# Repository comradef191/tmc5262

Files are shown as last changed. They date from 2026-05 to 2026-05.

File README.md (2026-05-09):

# TMC5262
This repository contains KiCAD 10.0 files for two stepper-motor driver boards based on the Trinamic [TMC5262](https://www.analog.com/en/products/tmc5262.html) driver.

**Notice:** As of May 9th 2026, these boards have not yet been tested. The initial release of these boards contains the text 'PROTOTYPE' on the silkscreen to reflect this.

You will have errors on opening the files if you do not have the [nasin-nanpa font](https://github.com/ETBCOR/nasin-nanpa) installed, used by me for both marking my name and occasionally eastereggs.

These files contain LCSC P/Ns for the SMD components and, on the external board the two large capacitors. Specific P/Ns are not provided for other through-hole components.

While these files are intended to be compatible with JLCPCB assembly, as of May 9th 2026 only Digikey is [selling the driver IC](https://www.digikey.com/en/products/detail/analog-devices-inc-maxim-integrated/TMC5262AFV/29292344), thus you will have to solder this component yourself or consign the chips to JLCPCB.

## External Driver:
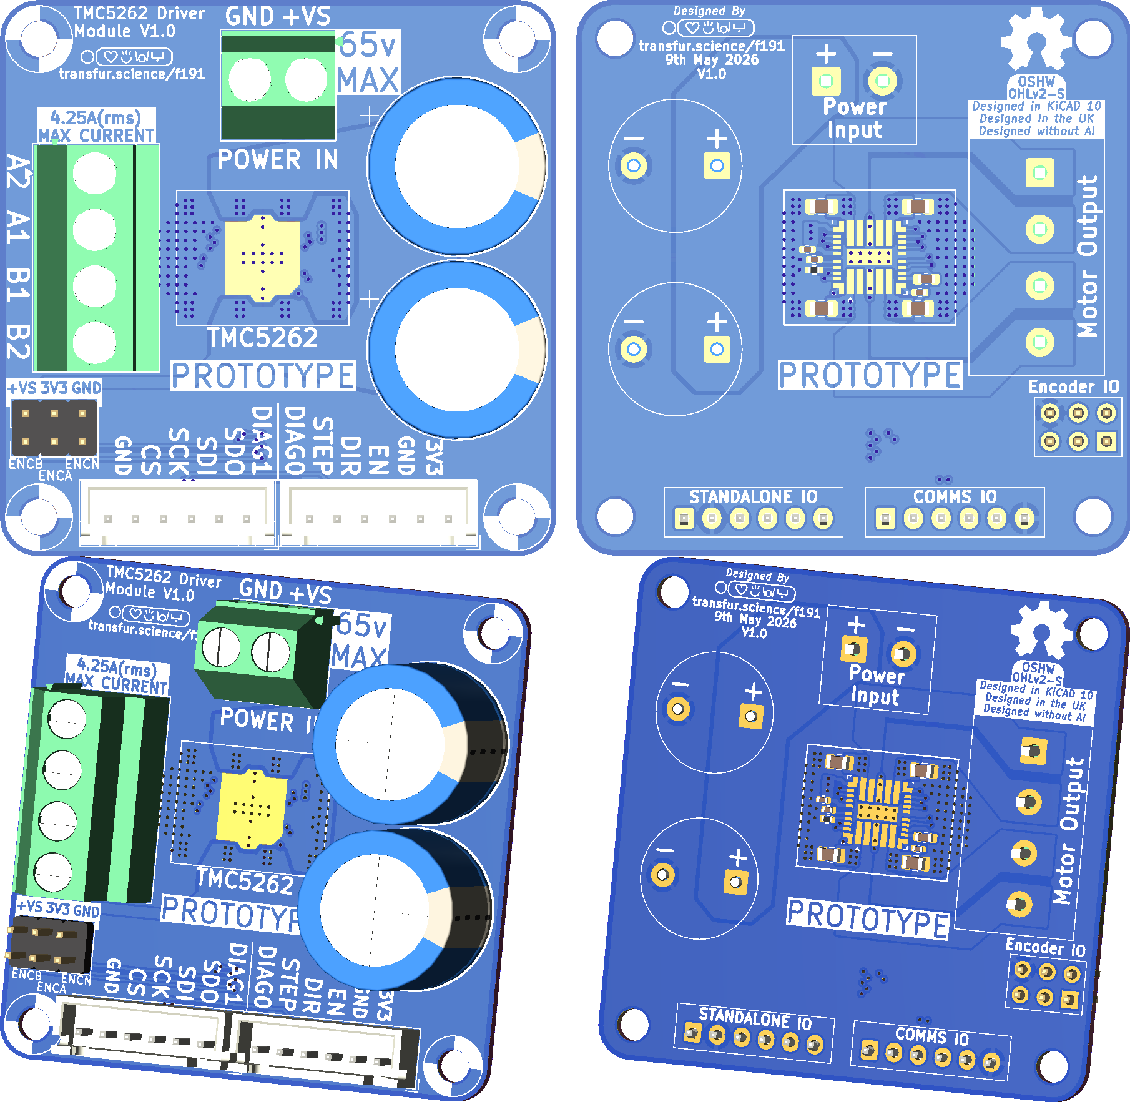
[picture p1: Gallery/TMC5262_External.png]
TMC5262_External

This is a larger board intended for fully-testing the driver and all its features.

The files for this board are located in the *'Motor-TMC5262-external'* directory.

- **Dimensions:** 50x50mm PCB, with 43x3mm M3 mounting holes.
-**Voltage Input:** 65v max, 1x2 5.08mm-Pitch screwterminal
- **Coil Output:** 4A max, 1x4 5.08mm-Pitch screwterminal
- **DIAG0 & DIAG1:** DIAG0 is on the 'STANDALONE IO' connector, DIAG1 is on the 'COMMS IO' connector. Connecting of both or either is not required.
- **Encoder:** ENCN, ENCA, ENCB pins broken-out to 2x3 header
- **Brake Resistor:** None built-in, use header to connect externally
- **Connectivity:** Connects to the MCU using two 6-pin JST-XH connectors

## Stepstick Driver:
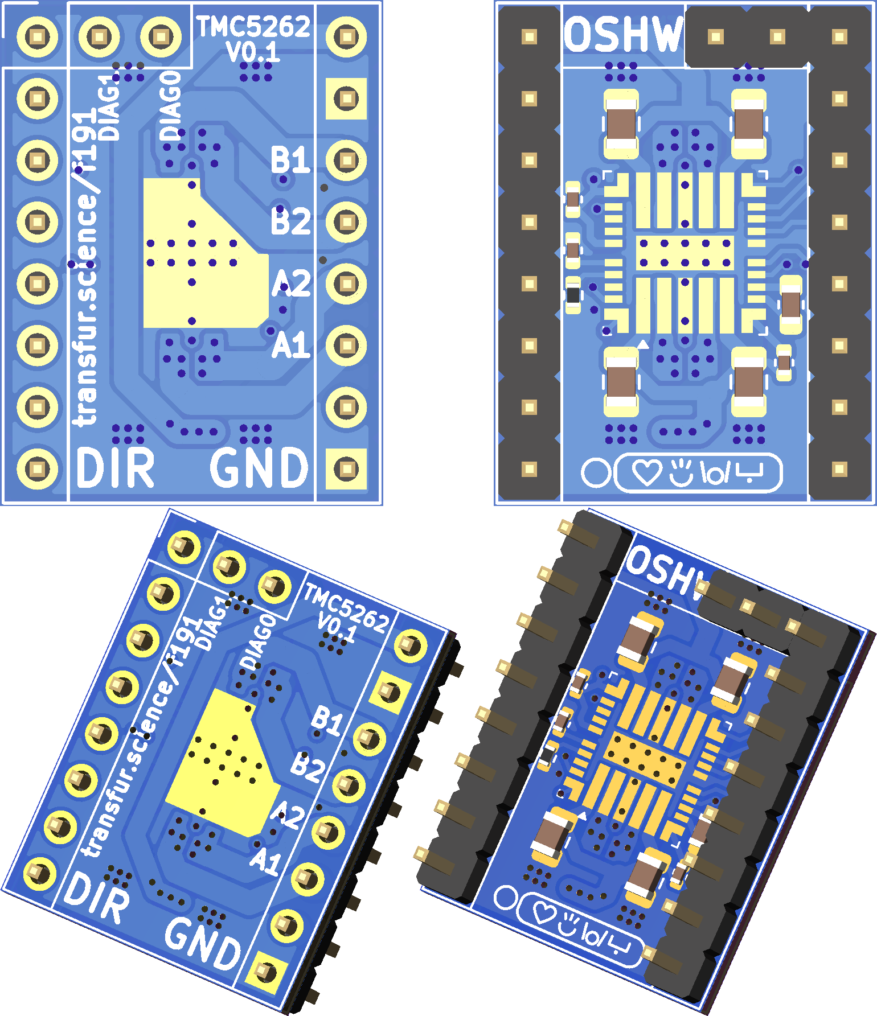
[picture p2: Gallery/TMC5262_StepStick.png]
TMC5262_StepStick

This is a small board intended for testing compatibility with existing stepstick-based mainboards, due to its smaller size caution to ensure no overheating should be taken.

The files for this board are located in the *'Motor-TMC5262-stepstick'* directory.

- **Dimensions:** 15.74x20.82mm StepStick
- **Voltage Input:** 65v max (Do not exceed rating of your mainboard)
- **Coil Output:** 3A max, B1/B2/A2/A1 instead of B2/A2/A1/B1
- **DIAG0 & DIAG1:** DIAG0 & DIAG1 connected per other StepSticks with two DIAG pins (e.g. [TMC22x SilentStepStick](https://learn.watterott.com/silentstepstick/pinconfig/))
- *Encoder:** Not-Present
- **Brake Resistor:** Not-Present
- **Connectivity:** Connects to the MCU using a standard 'StepStick' style socket. Make sure to set the jumpers to use SPI.

# License
This project is licensed under the CERN OHL V2 - S, see LICENSE.TXT for further information.

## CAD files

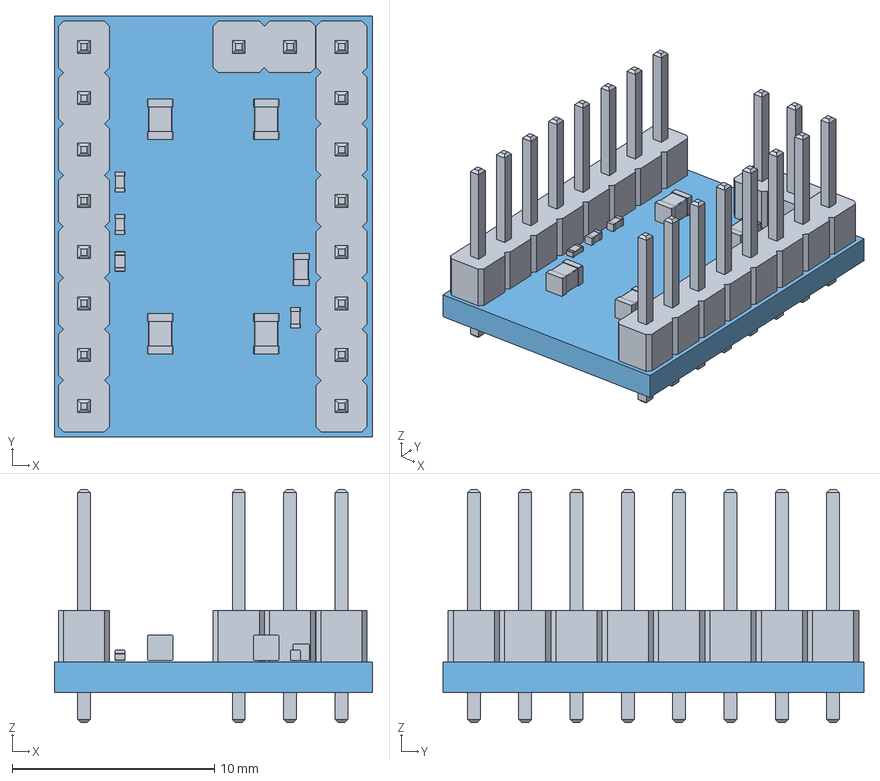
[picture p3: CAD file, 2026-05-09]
Resources/Motor-TMC5262-Stick.step
15.7 x 20.8 x 11.5 mm
C_0805_2012Metric x 4
C_0402_1005Metric x 3
C_0603_1608Metric
R_0402_1005Metric
PinHeader_1x08_P2.54mm_Vertical x 2
PinHeader_1x02_P2.54mm_Vertical
Motor-TMC5262-Stick_PCB

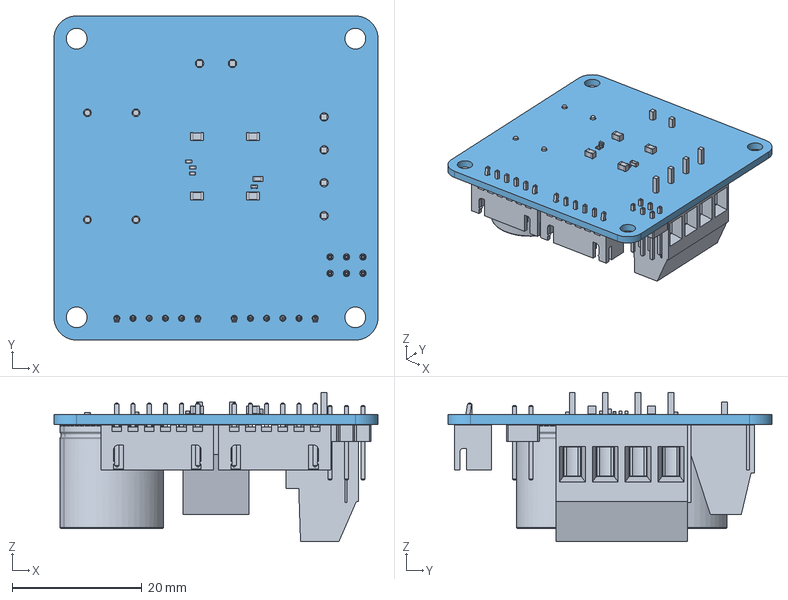
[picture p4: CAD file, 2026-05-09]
Resources/Motor-TMC5262-board.step
50.0 x 50.0 x 23.0 mm
C_0805_2012Metric x 4
C_0402_1005Metric x 3
C_0603_1608Metric
R_0402_1005Metric
JST_XH_B6B-XH-A_1x06_P2.50mm_Vertical x 2
CP_Radial_D16.0mm_P7.50mm x 2
TerminalBlock_Phoenix_MKDS-3-4-5.08_1x04_P5.08mm_Horizontal
PinHeader_2x03_P2.54mm_Vertical
TerminalBlock_Phoenix_MKDS-1,5-2-5.08_1x02_P5.08mm_Horizontal
Motor-TMC5262-board_PCB

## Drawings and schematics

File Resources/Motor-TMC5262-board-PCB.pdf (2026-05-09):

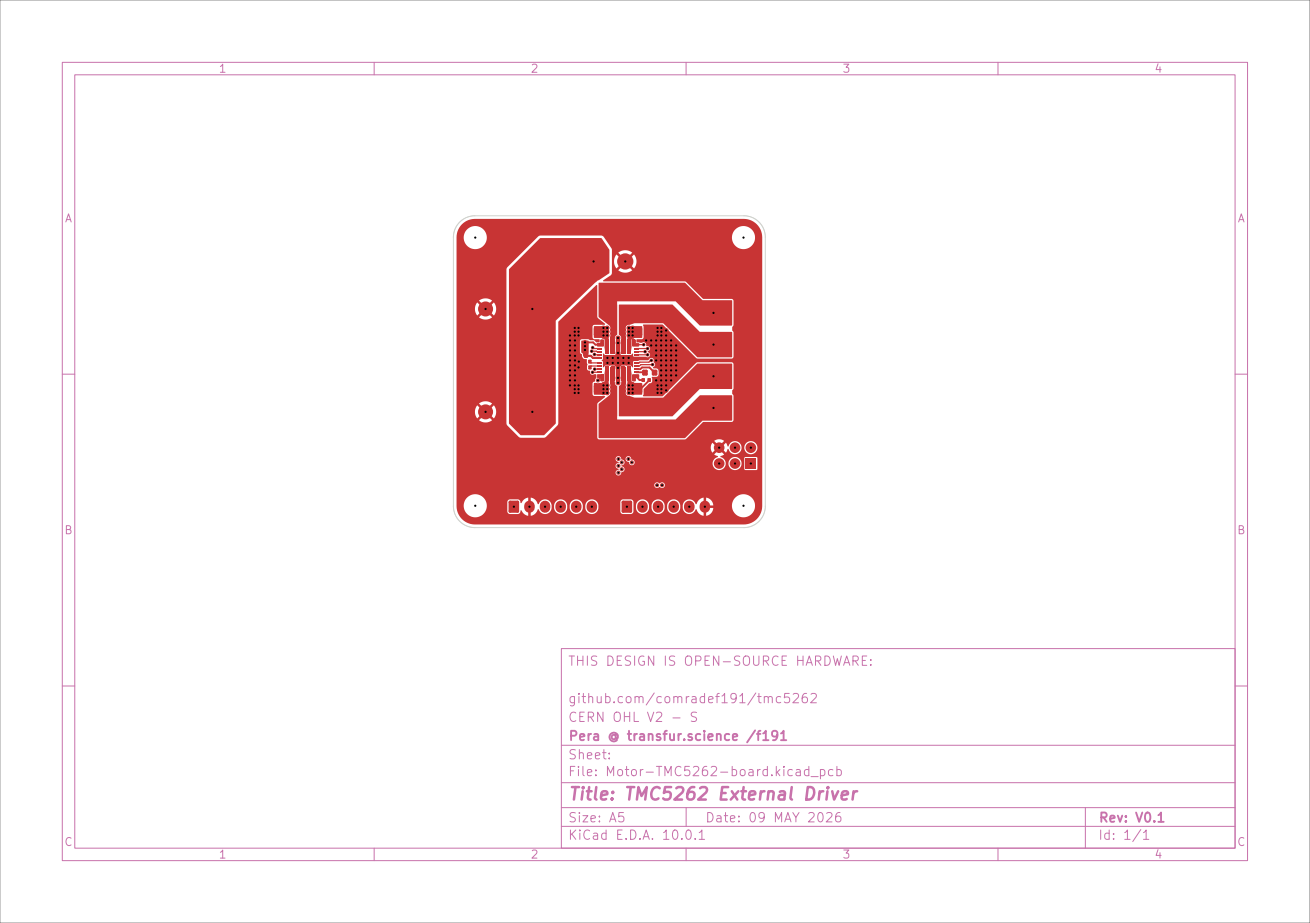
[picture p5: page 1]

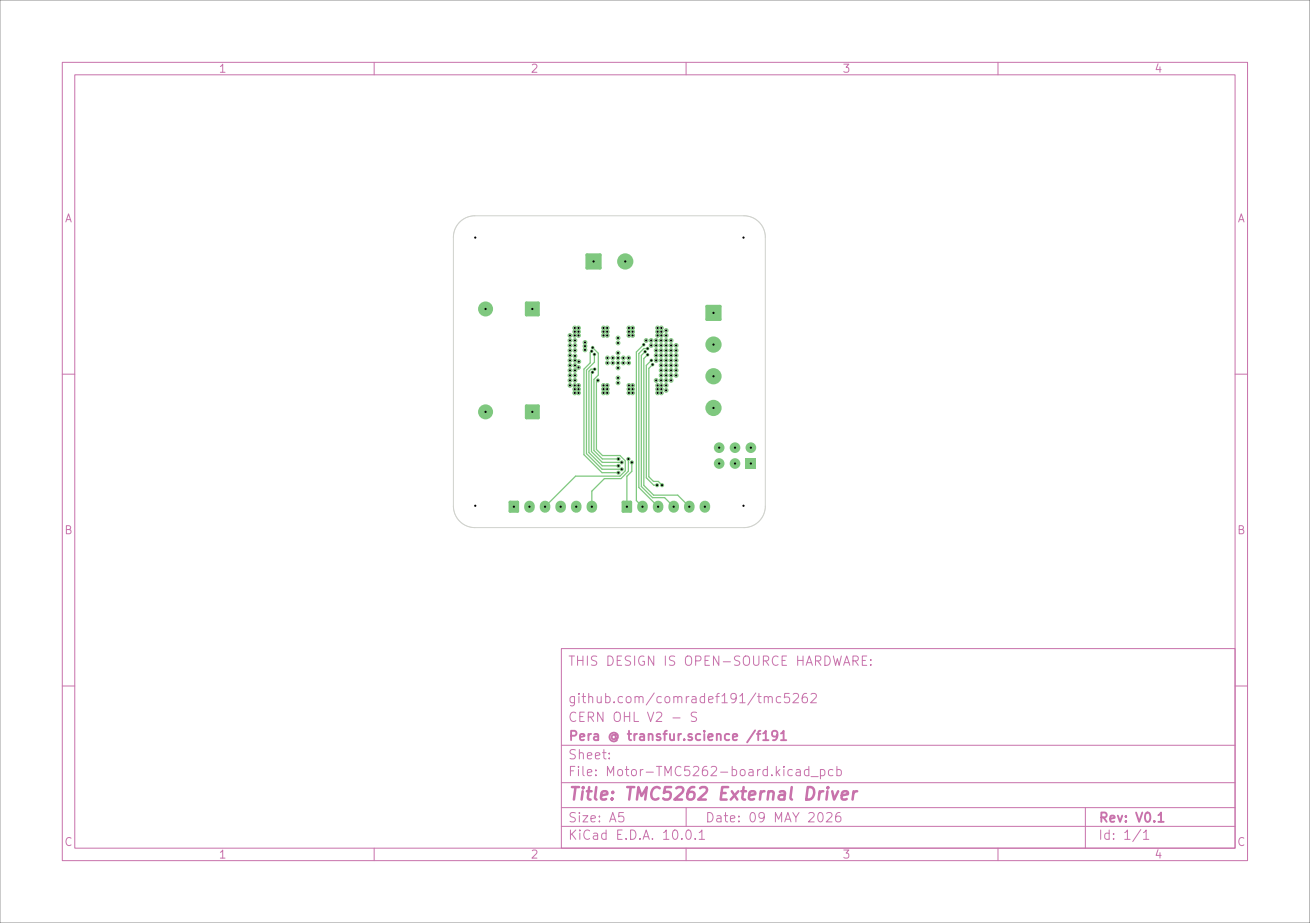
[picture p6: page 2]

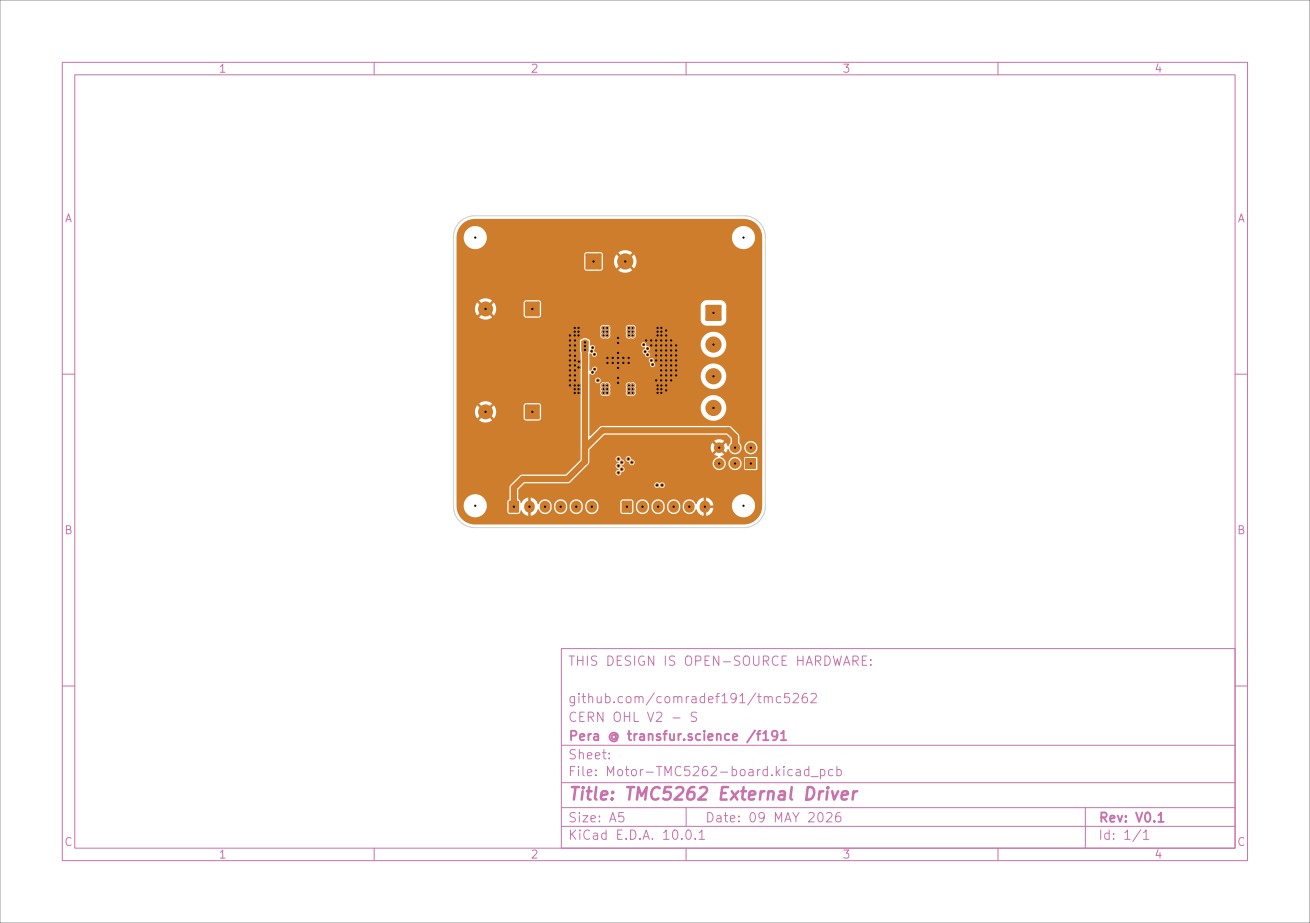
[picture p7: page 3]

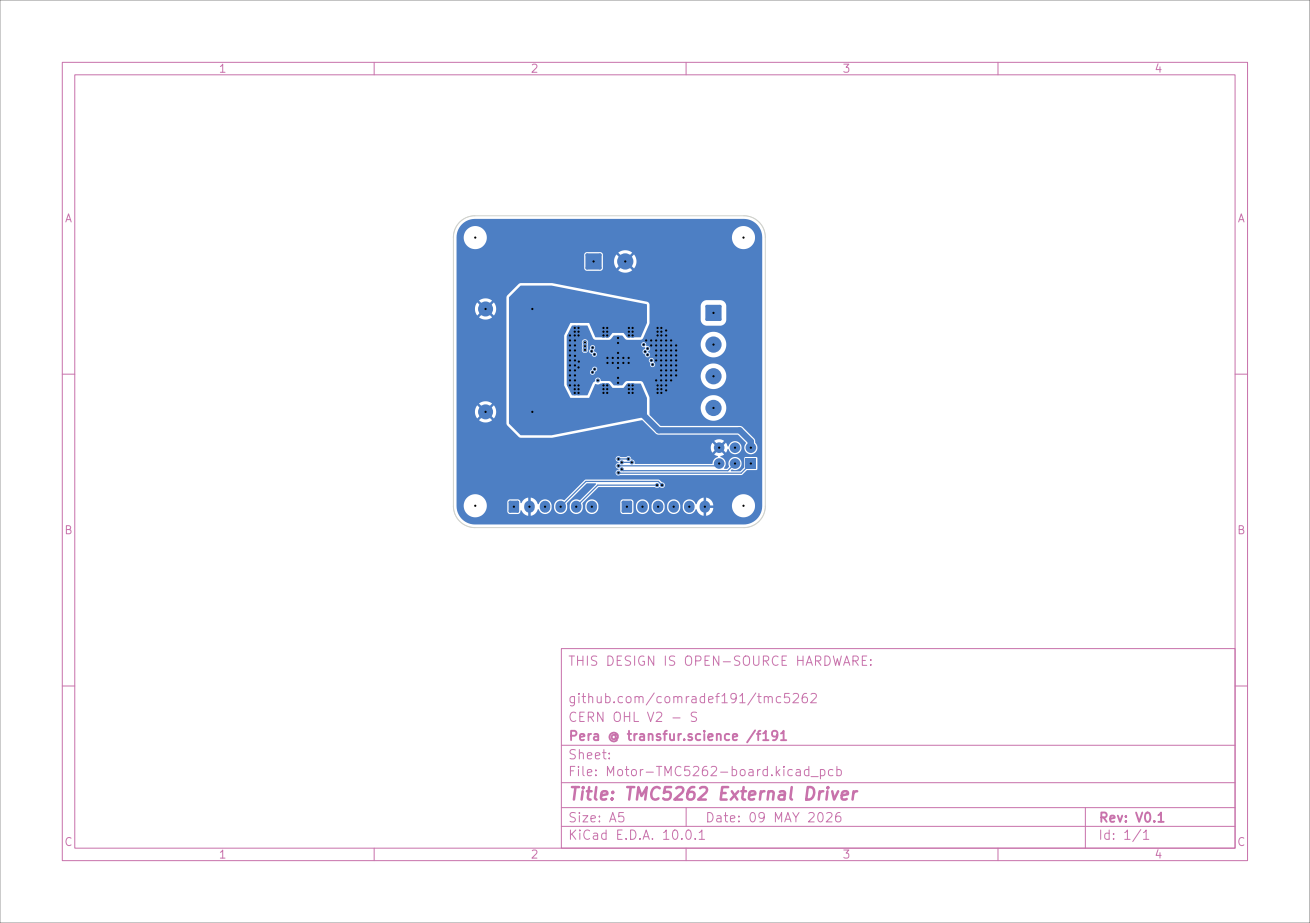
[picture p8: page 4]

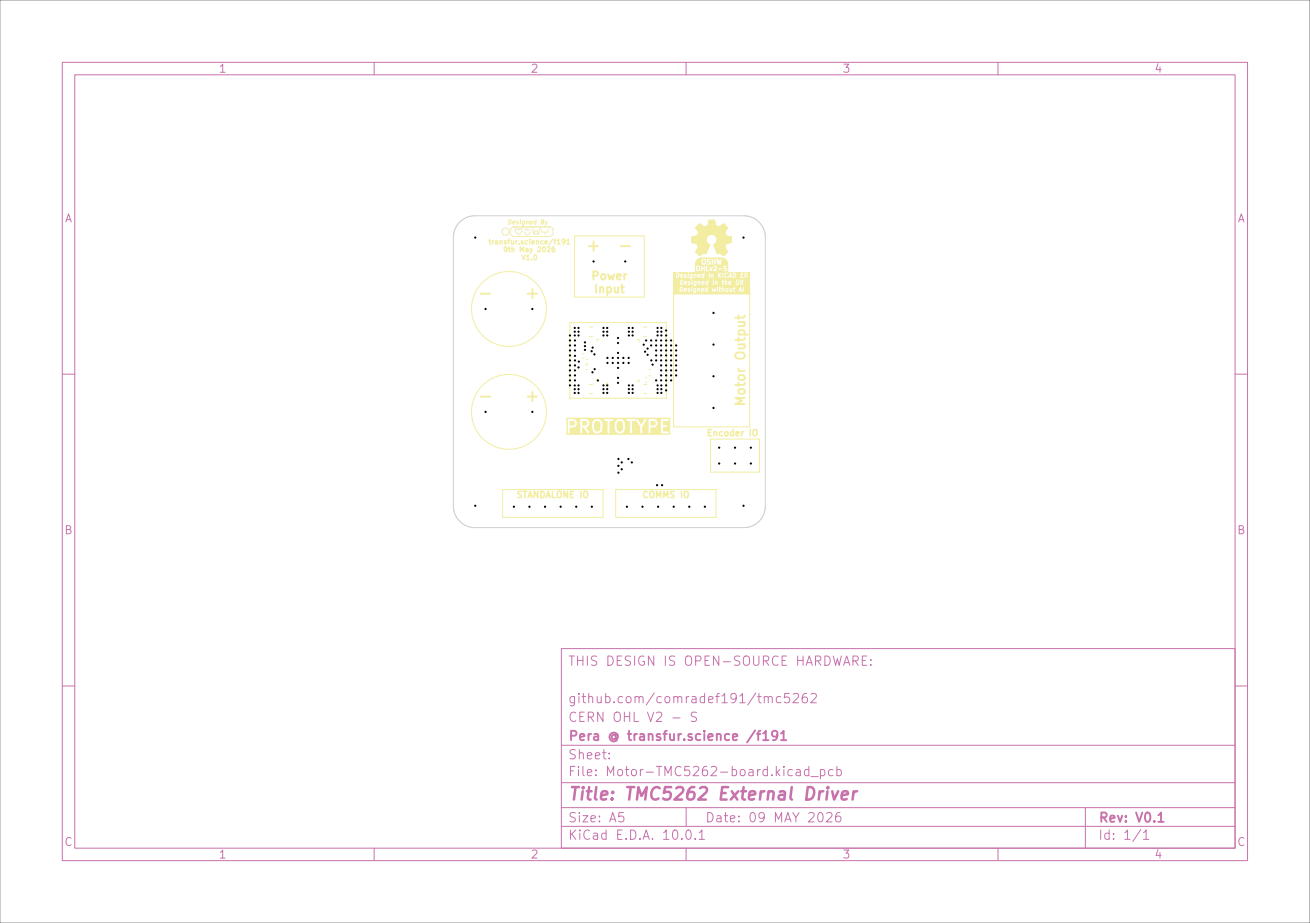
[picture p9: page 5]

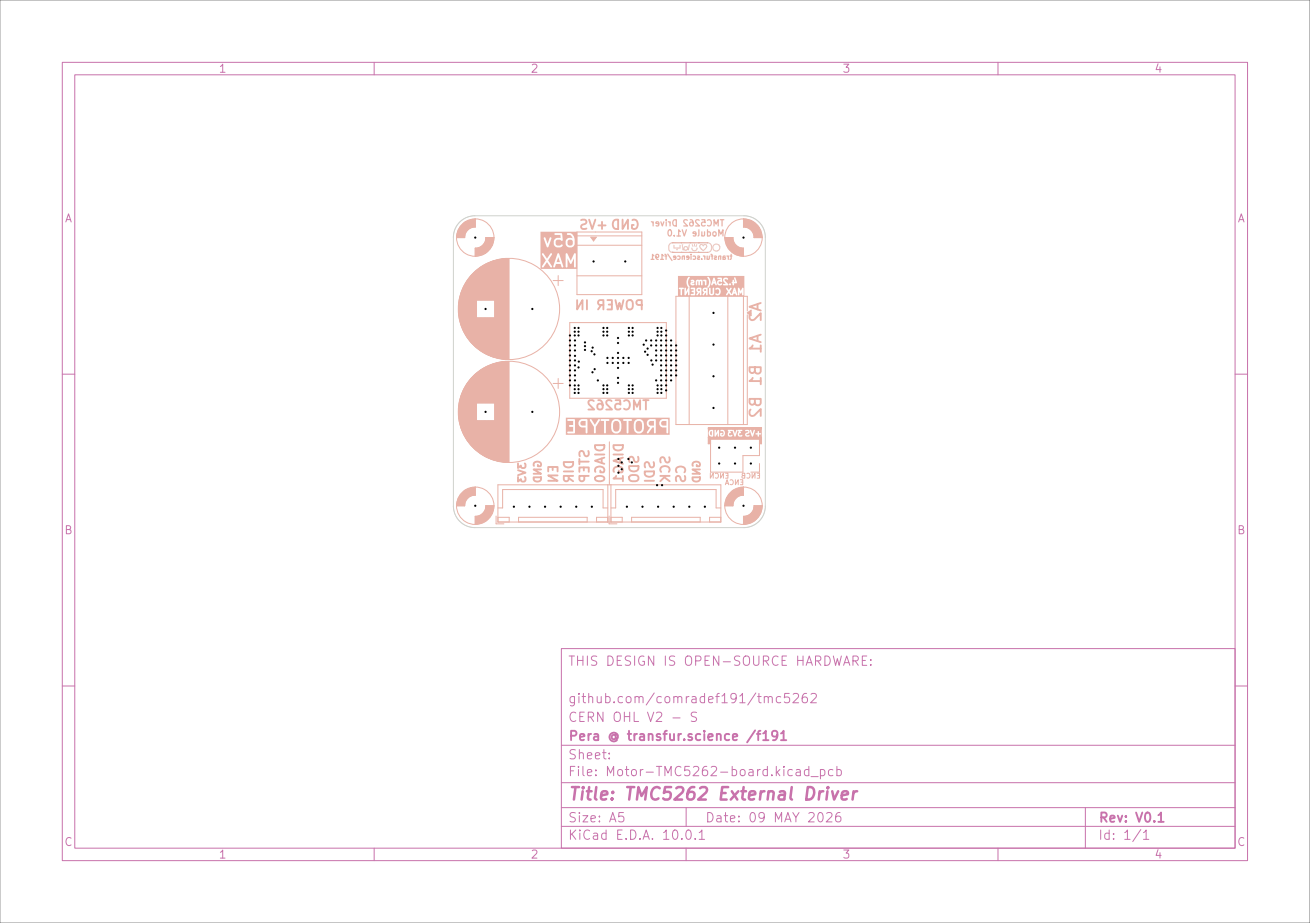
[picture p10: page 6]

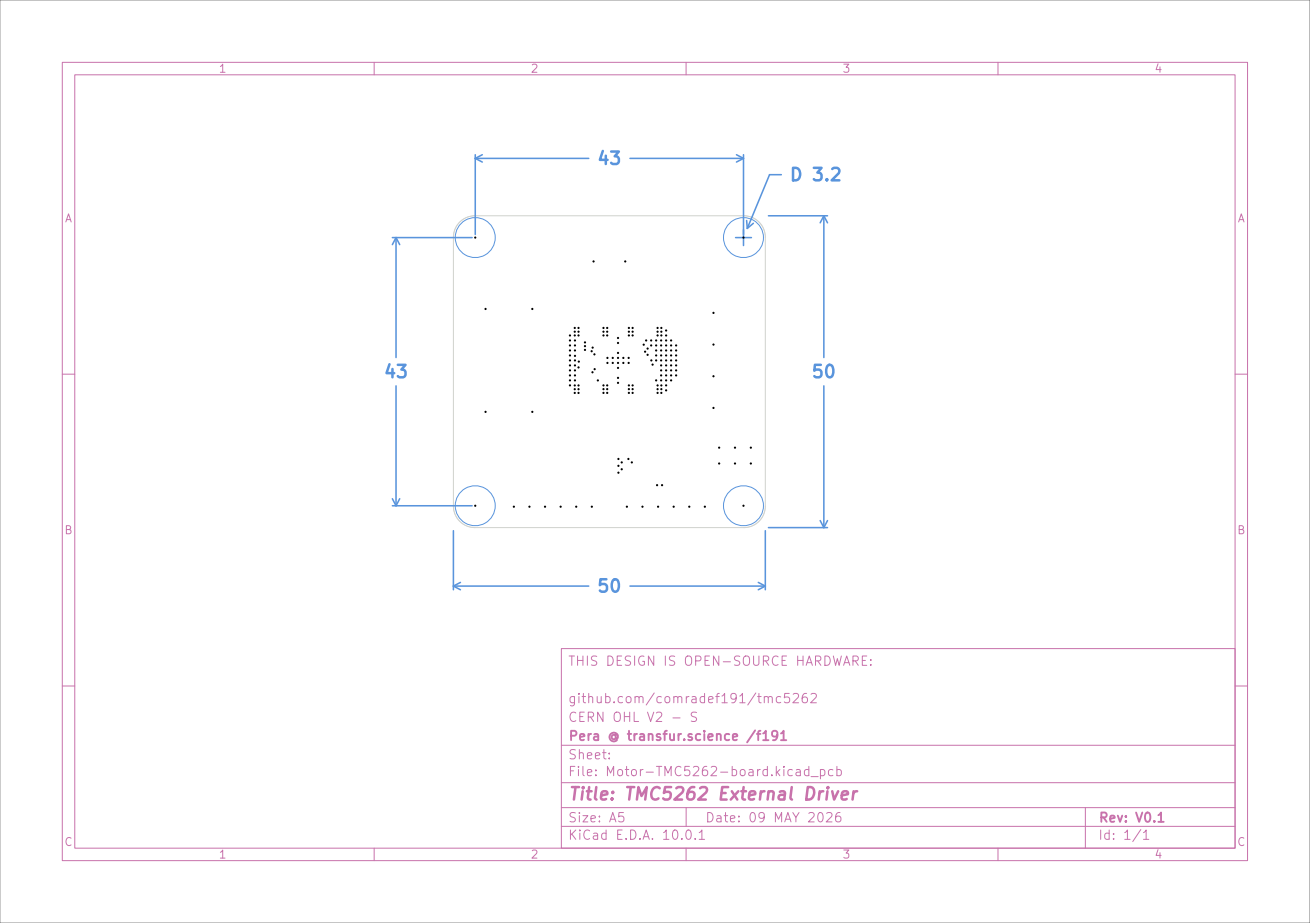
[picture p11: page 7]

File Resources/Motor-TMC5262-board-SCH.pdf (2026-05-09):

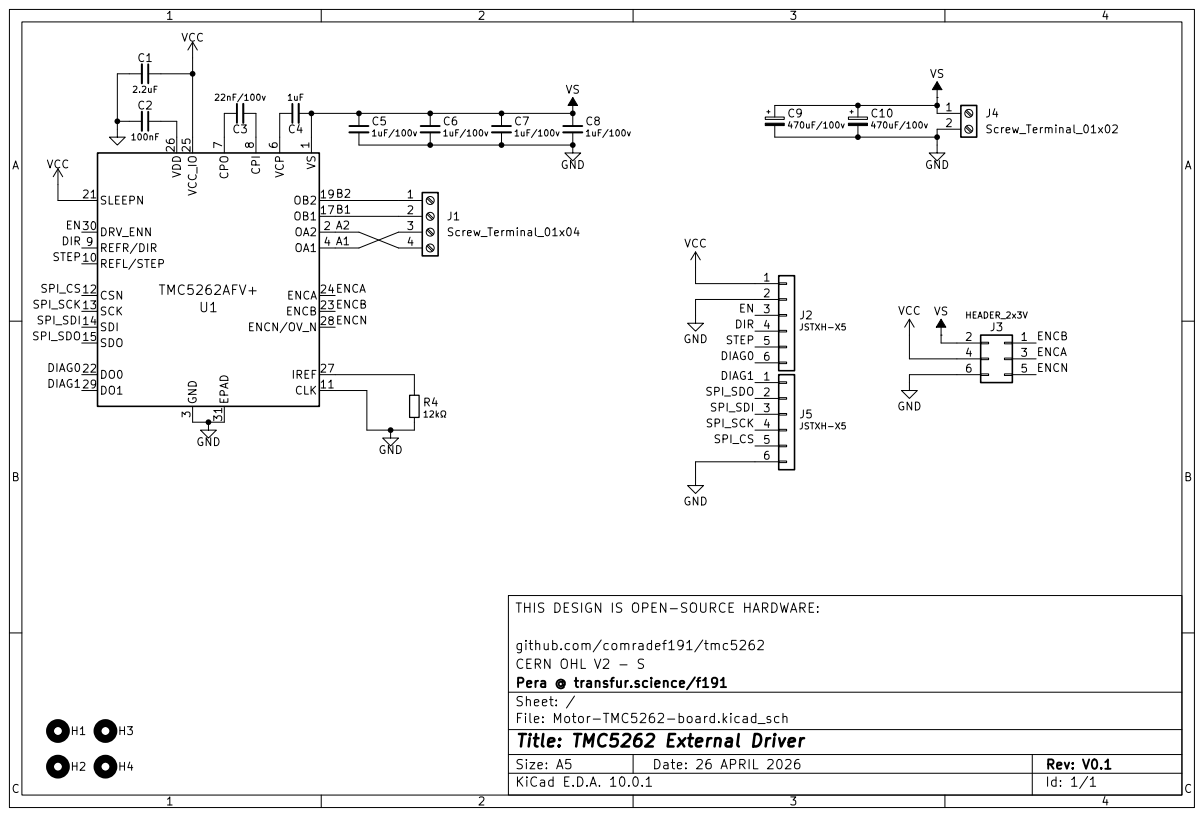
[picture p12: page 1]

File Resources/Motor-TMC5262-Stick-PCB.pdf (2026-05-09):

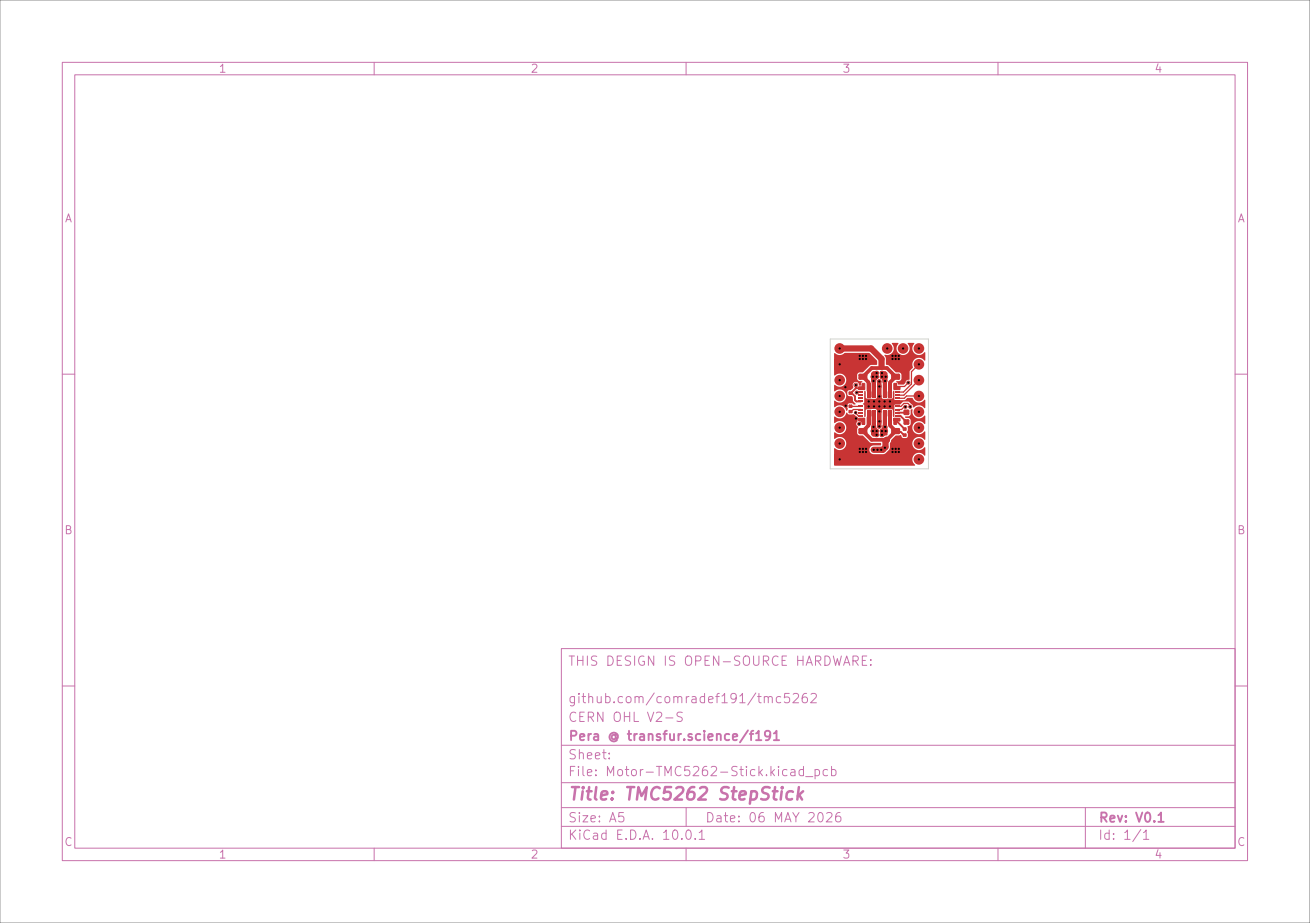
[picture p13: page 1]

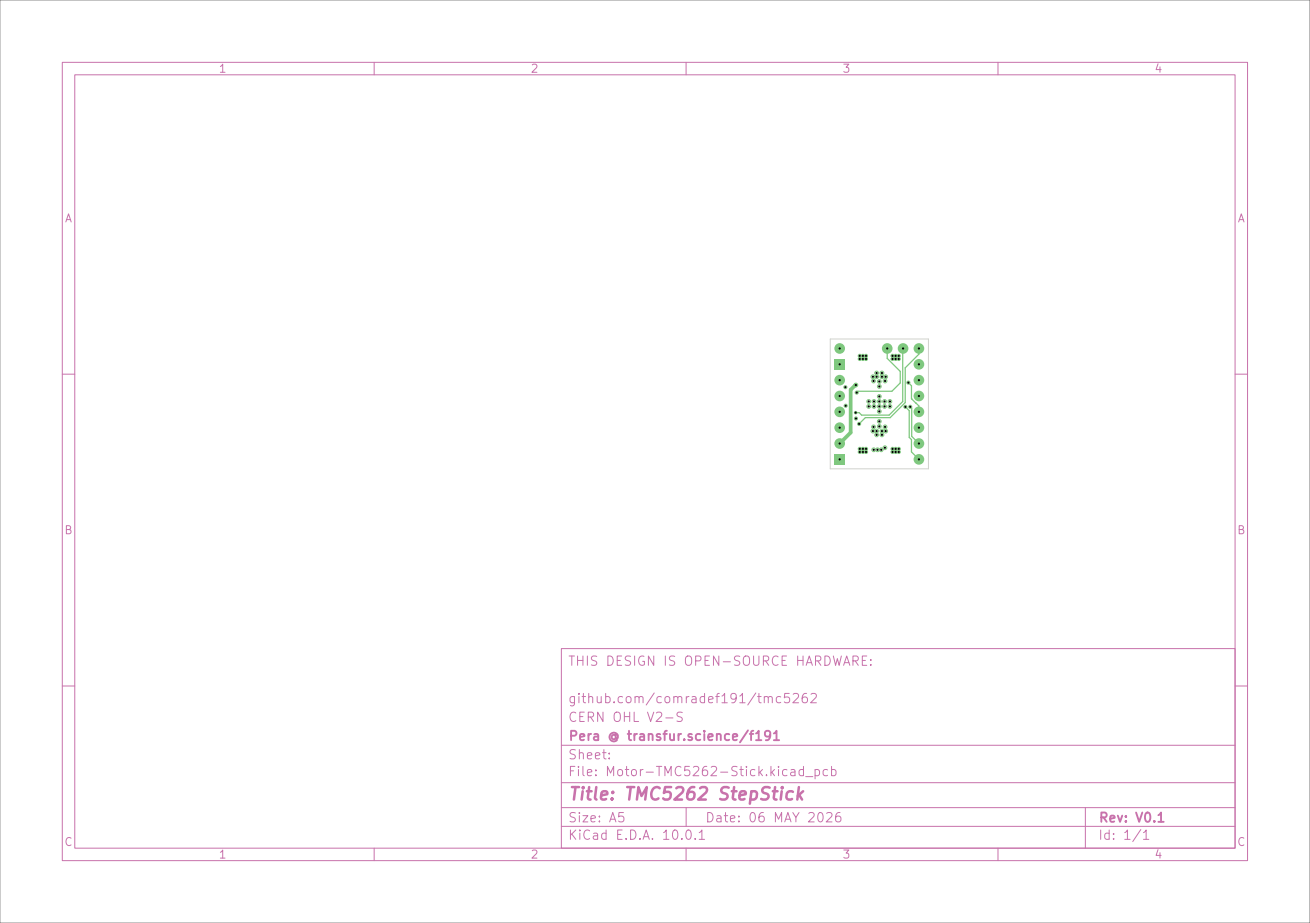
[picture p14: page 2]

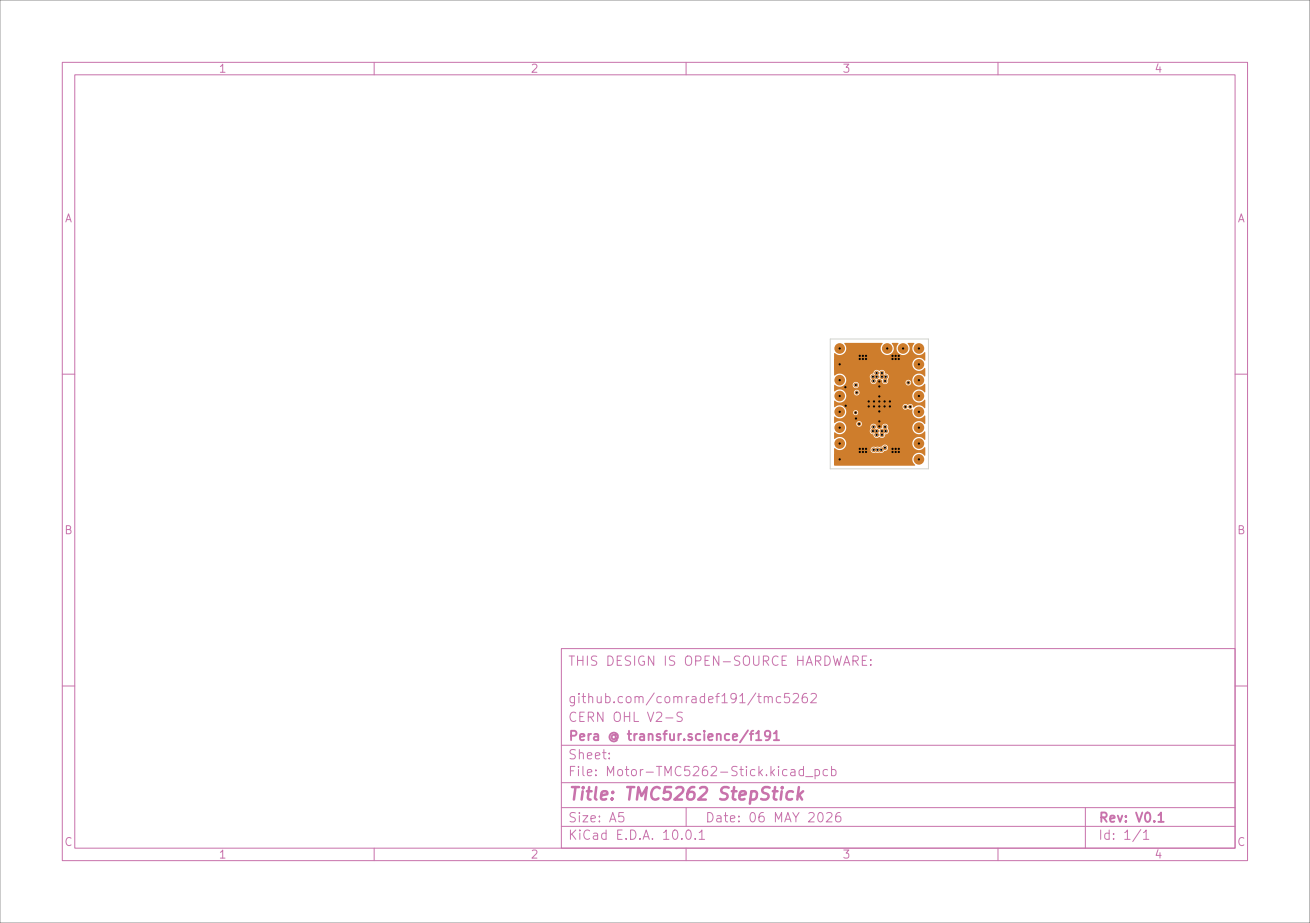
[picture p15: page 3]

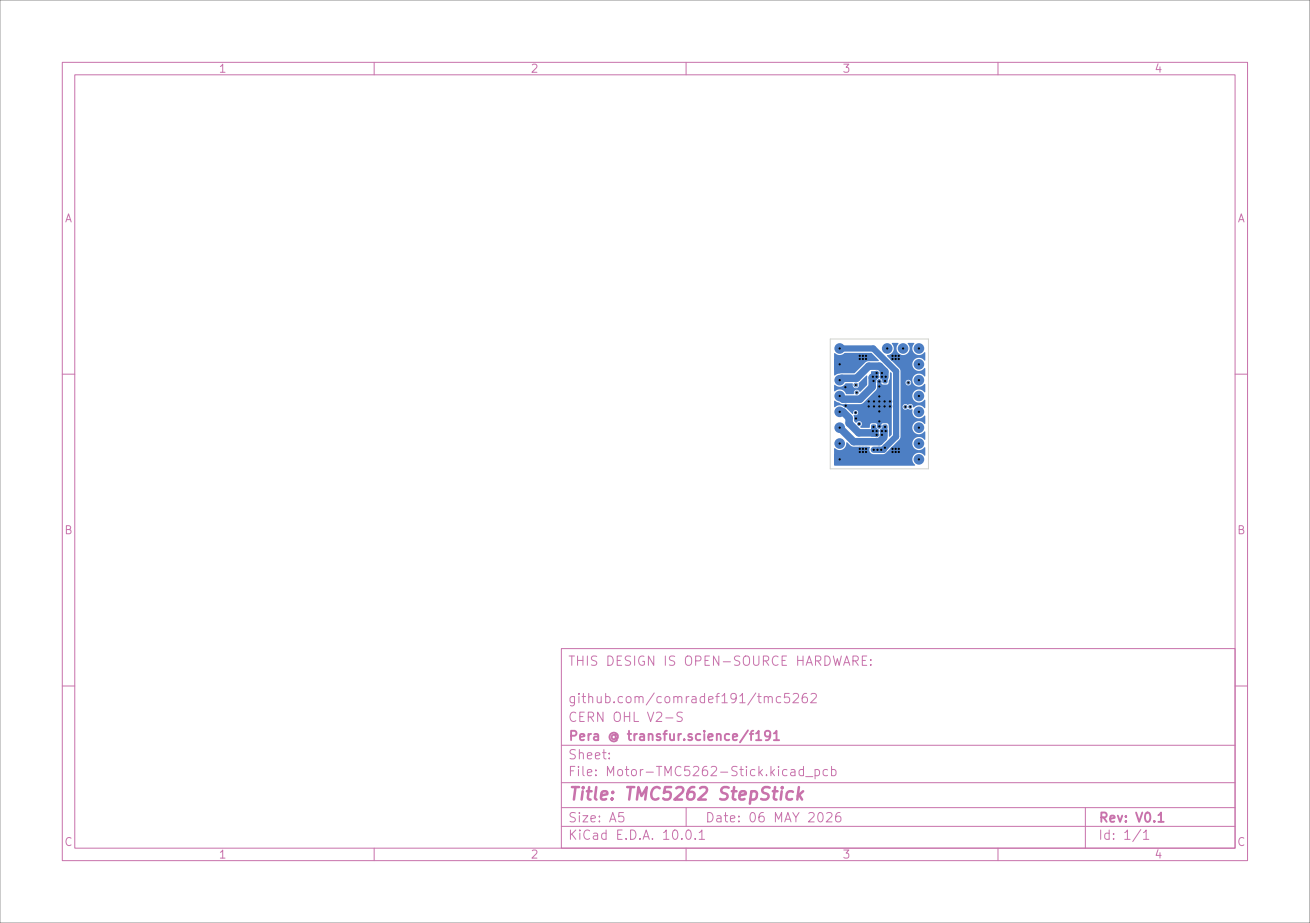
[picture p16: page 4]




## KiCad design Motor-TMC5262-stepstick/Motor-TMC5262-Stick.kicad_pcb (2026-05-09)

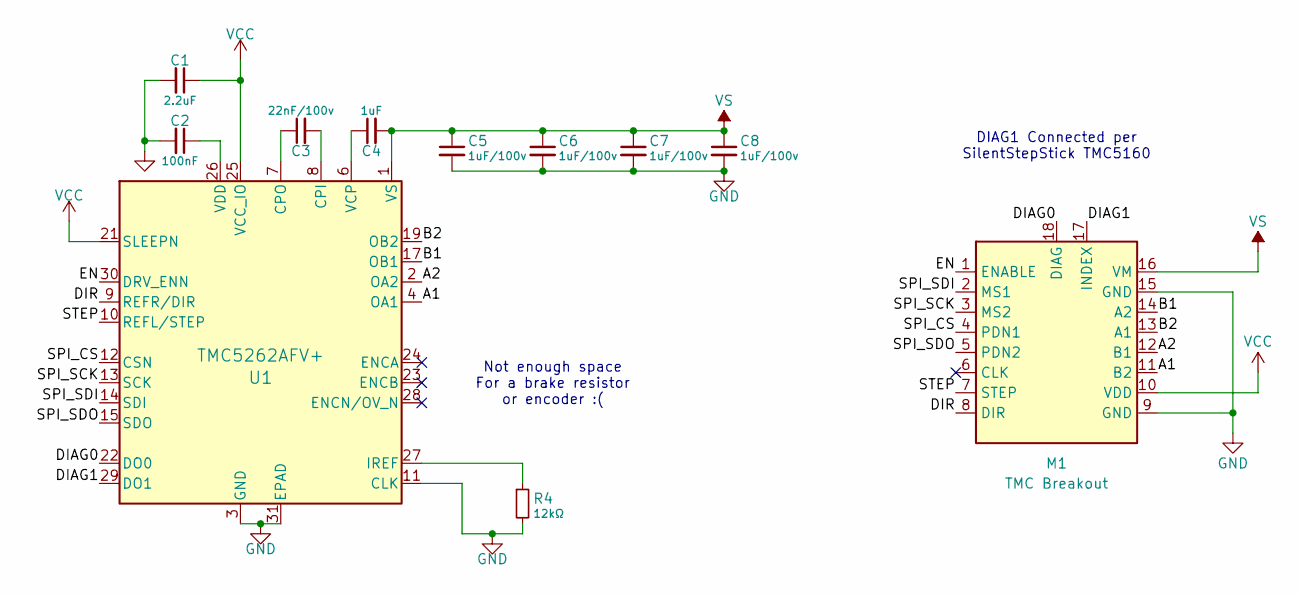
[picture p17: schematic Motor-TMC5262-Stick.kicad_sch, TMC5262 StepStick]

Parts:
C1: 2.2uF; C_0402_1005Metric; LCSC C12530
C2: 100nF; C_0402_1005Metric; LCSC C1525
C3: 22nF/100v; C_0603_1608Metric; LCSC C161234
C4: 1uF; C_0402_1005Metric; LCSC C52923
C5, C6, C7, C8: 1uF/100v; C_0805_2012Metric; LCSC C6119928
M1: TMC Breakout; TMC2209 Footprint (Plug)
R4: 12kΩ; R_0402_1005Metric; LCSC C25752
U1: TMC5262AFV+; 30L FC2QFN 6x6 (TMC5262); LCSC C9900140256

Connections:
/A1: M1.11 (B2), U1.4 (OA1)
/A2: M1.12 (B1), U1.2 (OA2)
/B1: M1.14 (A2), U1.17 (OB1)
/B2: M1.13 (A1), U1.19 (OB2)
/DIAG0: M1.18 (DIAG), U1.22 (DO0)
/DIAG1: M1.17 (INDEX), U1.29 (DO1)
/DIR: M1.8 (DIR), U1.9 (REFR/DIR)
/EN: M1.1 (ENABLE), U1.30 (DRV_ENN)
/SPI_CS: M1.4 (PDN1), U1.12 (CSN)
/SPI_SCK: M1.3 (MS2), U1.13 (SCK)
/SPI_SDI: M1.2 (MS1), U1.14 (SDI)
/SPI_SDO: M1.5 (PDN2), U1.15 (SDO)
/STEP: M1.7 (STEP), U1.10 (REFL/STEP)
GND: C1.2, C2.2, C5.2, C6.2, C7.2, C8.2, M1.9 (GND), M1.15 (GND), R4.2, U1.3 (GND), U1.11 (CLK), U1.18 (GND), U1.31 (EPAD)
unnamed: C3.2, U1.8 (CPI)
unnamed: C3.1, U1.7 (CPO)
unnamed: R4.1, U1.27 (IREF)
unnamed: C4.1, U1.6 (VCP)
unnamed: C2.1, U1.26 (VDD)
VCC: C1.1, M1.10 (VDD), U1.21 (SLEEPN), U1.25 (VCC_IO)
VS: C4.2, C5.1, C6.1, C7.1, C8.1, M1.16 (VM), U1.1 (VS), U1.5 (VS), U1.16 (VS), U1.20 (VS)

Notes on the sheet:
Not enough space For a brake resistor or encoder :(
DIAG1 Connected per SilentStepStick TMC5160

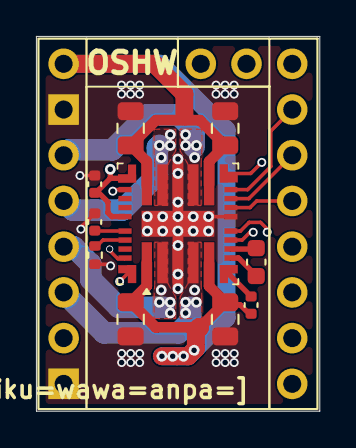
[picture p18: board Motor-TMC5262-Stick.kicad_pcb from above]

Board: 4 copper layers, 15.7 x 20.8 mm, 11 parts (1 on the bottom side), 21 nets.

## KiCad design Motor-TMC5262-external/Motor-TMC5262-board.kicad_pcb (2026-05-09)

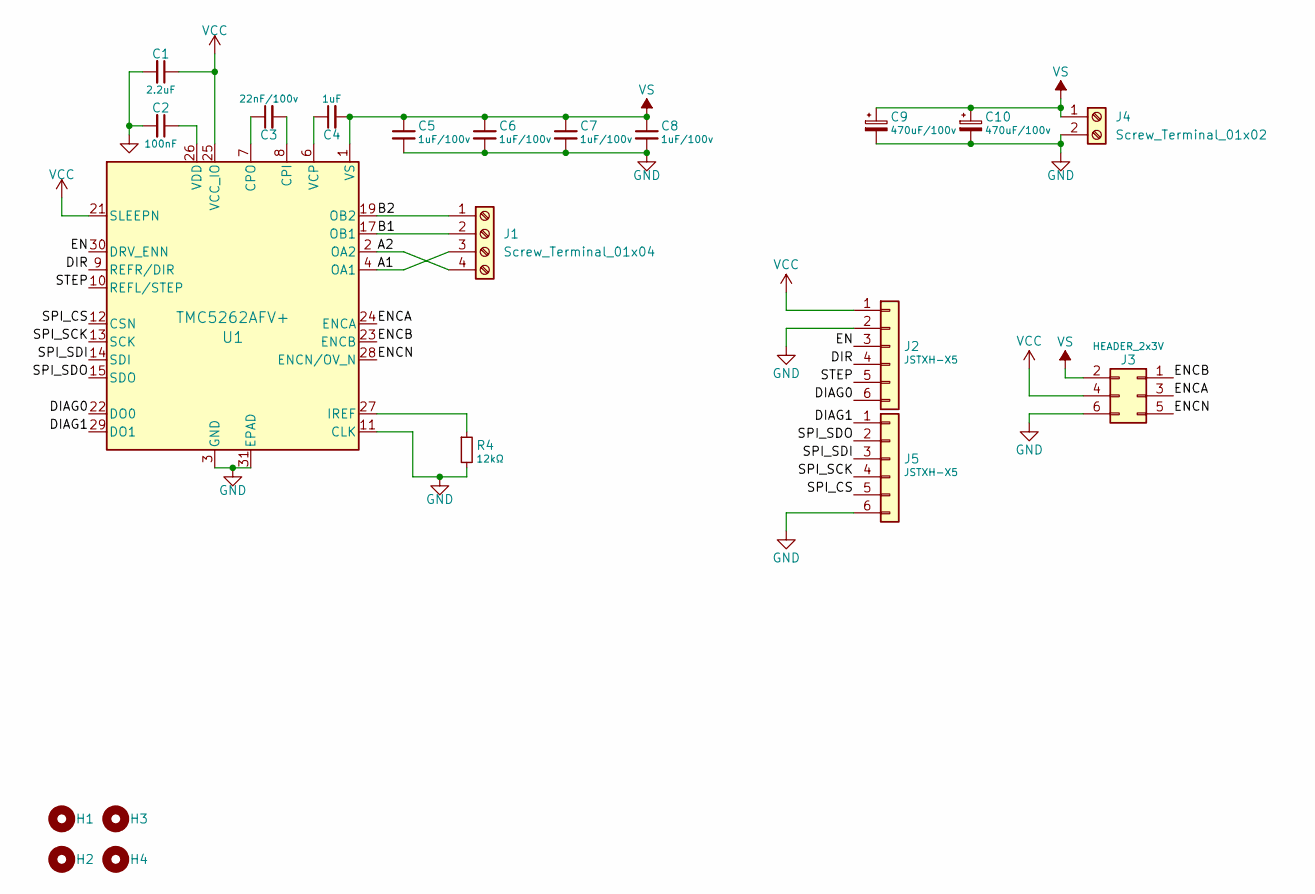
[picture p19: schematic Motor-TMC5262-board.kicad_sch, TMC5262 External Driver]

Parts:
C1: 2.2uF; C_0402_1005Metric; LCSC C12530
C2: 100nF; C_0402_1005Metric; LCSC C1525
C3: 22nF/100v; C_0603_1608Metric; LCSC C161234
C4: 1uF; C_0402_1005Metric; LCSC C52923
C5, C6, C7, C8: 1uF/100v; C_0805_2012Metric; LCSC C6119928
C9, C10: 470uF/100v; CP_Radial_D16.0mm_P7.50mm; LCSC C2913975
H1, H2, H3, H4: MountingHole; M3 Mounting Hole ~ Classic - No Keepout
J1: Screw_Terminal_01x04; TerminalBlock_Phoenix_MKDS-3-4-5.08_1x04_P5.08mm_Horizontal
J2, J5: JSTXH-X5; JST_XH_B6B-XH-A_1x06_P2.50mm_Vertical
J3: HEADER_2x3V; PinHeader_2x03_P2.54mm_Vertical
J4: Screw_Terminal_01x02; TerminalBlock_Phoenix_MKDS-1,5-2-5.08_1x02_P5.08mm_Horizont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
R4: 12kΩ; R_0402_1005Metric; LCSC C25752
U1: TMC5262AFV+; 30L FC2QFN 6x6 (TMC5262); LCSC C9900140256

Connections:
/A1: J1.3, U1.4 (OA1)
/A2: J1.4, U1.2 (OA2)
/B1: J1.2, U1.17 (OB1)
/B2: J1.1, U1.19 (OB2)
/DIAG0: J2.6, U1.22 (DO0)
/DIAG1: J5.1, U1.29 (DO1)
/DIR: J2.4, U1.9 (REFR/DIR)
/EN: J2.3, U1.30 (DRV_ENN)
/ENCA: J3.3, U1.24 (ENCA)
/ENCB: J3.1, U1.23 (ENCB)
/ENCN: J3.5, U1.28 (ENCN/OV_N)
/SPI_CS: J5.5, U1.12 (CSN)
/SPI_SCK: J5.4, U1.13 (SCK)
/SPI_SDI: J5.3, U1.14 (SDI)
/SPI_SDO: J5.2, U1.15 (SDO)
/STEP: J2.5, U1.10 (REFL/STEP)
GND: C1.2, C2.2, C5.2, C6.2, C7.2, C8.2, C9.2, C10.2, J2.2, J3.6, J4.2, J5.6, R4.2, U1.3 (GND), U1.11 (CLK), U1.18 (GND), U1.31 (EPAD)
unnamed: C3.2, U1.8 (CPI)
unnamed: C3.1, U1.7 (CPO)
unnamed: R4.1, U1.27 (IREF)
unnamed: C4.1, U1.6 (VCP)
unnamed: C2.1, U1.26 (VDD)
VCC: C1.1, J2.1, J3.4, U1.21 (SLEEPN), U1.25 (VCC_IO)
VS: C4.2, C5.1, C6.1, C7.1, C8.1, C9.1, C10.1, J3.2, J4.1, U1.1 (VS), U1.5 (VS), U1.16 (VS), U1.20 (VS)

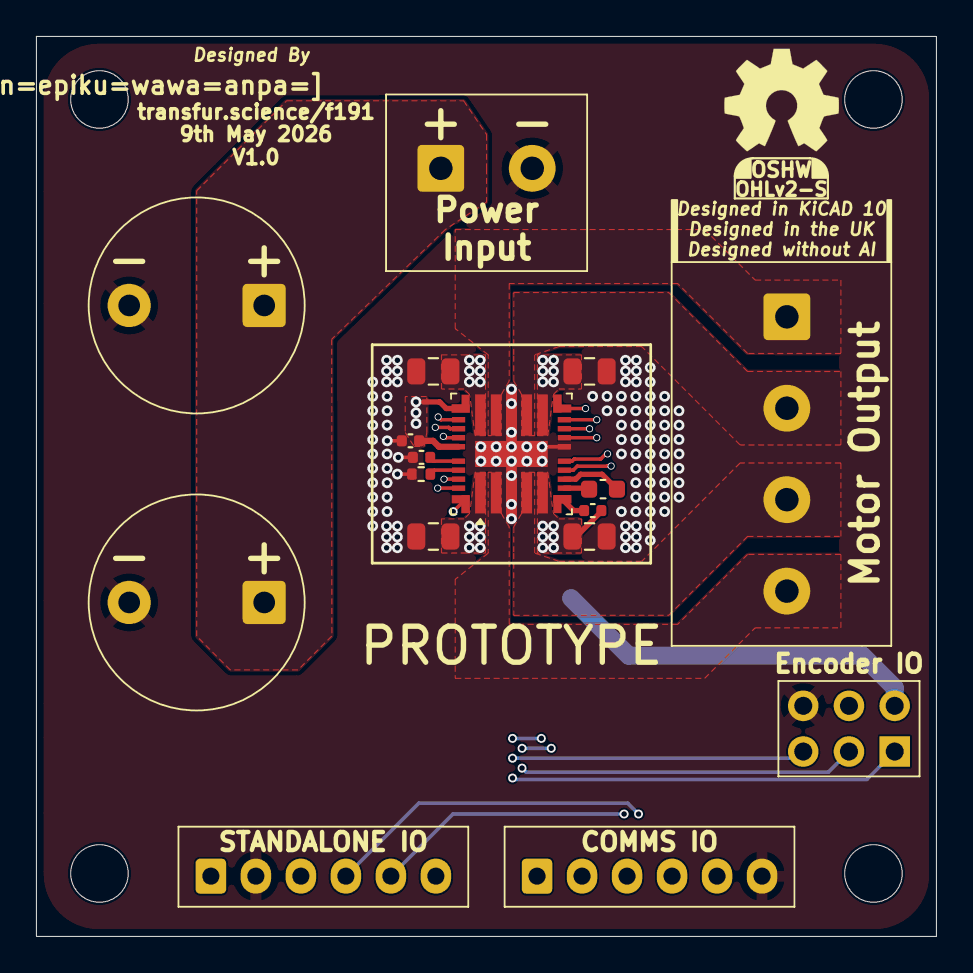
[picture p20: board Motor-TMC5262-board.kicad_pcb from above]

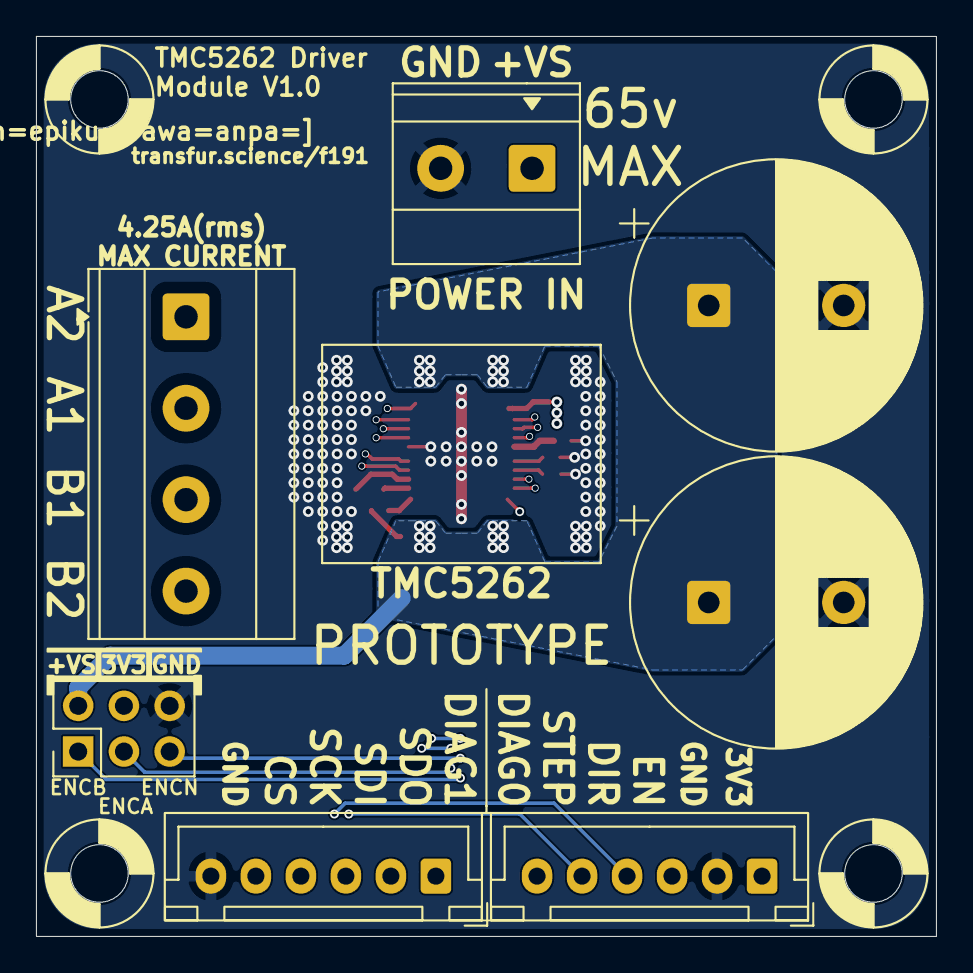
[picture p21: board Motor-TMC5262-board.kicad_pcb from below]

Board: 4 copper layers, 50.0 x 50.0 mm, 21 parts (11 on the bottom side), 24 nets.
